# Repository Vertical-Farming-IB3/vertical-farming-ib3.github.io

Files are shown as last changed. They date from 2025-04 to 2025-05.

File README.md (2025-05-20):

# IB3 Plan-T pages site

Deze website is bedoeld voor het bijhouden van de voortgang van het project IB3.
De website is ontworpen en bijgehouden door de studenten BA3ecfs en S2ecfs, en is bedoeld voor alle geïnteresseerden in het vertical farming project. Het is een stappenplan van de huidige realisatie en een presentatie van de behaalde resultaten.

[Project website](https://vertical-farming-ib3.github.io/)

[Link](https://github.com/Vertical-Farming-IB3/Plan-T) naar de hoofdrepository.

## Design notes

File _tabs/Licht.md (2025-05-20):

---
icon: fas fa-lightbulb
order: 3
---

## Inhoud
1. [Introductie](#introductie)
2. [led-selectie](#led-selectie)
3. [Spectrum en kleurverhouding](#spectrum-en-kleurverhouding)
    - [Blauw licht (450-460 nm)](#blauw-licht)
    - [Rood licht (560-670 nm)](#rood-licht)
    - [Far-red licht (720-740 nm)](#far-red-licht)
    - [Photosynthetic Photon Flux Density (PPFD)](#photosynthetic-photon-flux-density-ppfd)
        * [Sla en basilicum](#sla-en-basilicum)
        * [Koriander](#koriander)
        * [PPFD-berekening](#ppfd-berekening)
4. [Elektrisch Dimensioneren](#elektrisch-dimensioneren)
5. [Aangeraden Instelling](#aangeraden-instelling) 
6. [Afstand en uniformiteit](#afstand-en-uniformiteit)
7. [Fotoperiode](#fotoperiode)
8. [Thermische berekeningen led-PCB](#thermische-berekeningen-led-pcb)
9. [Ontwerp](#ontwerp)
10. [Uitvoering](#uitvoering)
11. [Afgewerkt product](#afgewerkt-product)
11. [Bronnen](#bronnen)

## Introductie

Bij Team Licht werken we aan led-verlichtingssystemen die speciaal zijn afgestemd voor de vertical farm. Ons huidige project richt zich op de teelt van snijsla en groene kruiden zoals basilicum, koriander en munt. De nadruk ligt op een efficiënte systeem met voldoende Photosynthetic Photon Flux Density (PPFD), afgestemd op bladgroenten. 

## led-selectie

Om de juiste leds te bepalen hebben we ons gebaseerd op het uitgebreid onderzoek van vorig en de expertise van het team van Labo Licht. We hebben voor leds gekozen met een uniforme lichtverdeling voor optimale groei van de planten in de vertical farm. Zo zijn we uitgekomen bij de volgende Cree leds: 

| Type | Kleur | Golflengte (nm) | PPF (µmol/s⁻¹) | View Angle (°) |
|---|---|---|---|---|
| JE2835ARY  | Royal Blue  | 450–460 | 1.01 | 124 |
| JE2835AHR  | Photo Red | 650–670 | 0.72 | 121 |
| JE2835AFR  | Far-Red | 720–740 | 0.72 | 121 |

## Spectrum en kleurverhouding

De keuze van lichtkleuren is cruciaal voor het sturen van de fotosynthese, bladontwikkeling en
morfologie. Dit project gebruikt drie spectraalkleuren:

### Blauw licht (450–460 nm) {#blauw-licht}

Bevordert bladontwikkeling, fotomorfogenese, pigmentvorming en compactheid van de plant.
Het helpt overmatige strekking voorkomen door de plant laag te houden en de stengels stevig te maken.

### Rood licht (650–670 nm) {#rood-licht}

Stimuleert fotosynthese en draagt sterk bij aan biomassavorming. Rood licht is bijzonder efficiënt in de activering van chlorofyl.

### Far-Red licht (720–740 nm) {#far-red-licht}

Hoewel far-red licht buiten het fotosynthetisch actieve spectrum (PAR) valt, draagt het bij aan
het Emerson-effect, waarbij de combinatie van rood en far-red licht leidt tot een verhoogde
fotosynthetische efficiëntie [1]. In dit ontwerp wordt far-red licht daarom in beperkte mate
toegepast. Aangezien de focus ligt op bladgroei en niet op de reproductieve fase (zoals bloei of
zaadvorming), is het nodig om te veel Far-Red licht te vermijden. Een te hoog percentage van Far-Red 
licht zal het process van voortijdig schieten bevorderen, wat ongewenst is bij de teelt
van bladgewassen. De planten kunnen er ook zwak van worden om ze te snel in de hoogte zullen groeien en de stengels hierdoor te smal worden.

### Photosynthetic Photon Flux Density (PPFD)

PPFD, uitgedrukt in µmol m⁻² s⁻¹, meet het aantal fotosynthetisch actieve lichtfotonen dat een
plantoppervlak bereikt. Dit is essentieel in vertical farming, waar kunstlicht de enige bron van
energie is voor fotosynthese.

#### Sla en basilicum

- PPFD van 250 µmol m⁻² s⁻¹ is optimaal voor biomassa, kwaliteit en energiegebruik.
- 200 µmol m⁻² s⁻¹ volstaat bij hoge plantdichtheid (680 planten/m2).
- PPFD spectra verdeling: R:60% FR:20% BL:20% (Dit zijn **NIET** de waardes om in te stellen via HomeAssistant, zie verder)
  
#### Koriander

- PPFD van 250–300 µmol m⁻² s⁻¹ bevordert biomassatoename en antioxidantproductie.
- Optimale prestaties bij verhoogde worteltemperatuur en CO2.
- PPFD spectra verdeling: R:60% FR:20% BL:20% (Dit zijn **NIET** de waardes om in te stellen via HomeAssistant, zie verder)

Aanbevolen richtlijn: Voor bladgewassen is 200–250 µmol m⁻² s⁻¹ geschikt, afhankelijk vanruimtegebruik en teeltstrategie. Voor de verdeling van deze PPFD raden we volgend startpunt aan R:60% FR:20% BL:20% (dit komt **NIET** overeen met de procentuele waardes van de sliders op het Home Assistant dashboard! Zie "Aangeraden Instelling" voor meer info)

#### PPFD-berekening

Voor een en lade van 0.1 m² met 12 blauwe, 20 rode en 16 far-red leds geldt:

PPFD<sub>totaal</sub> = (12 × 1.01) + (20 × 0.72) + (16 × 0.76)  
= 12.12 + 14.4 + 12.16 = 38.68 µmol/s  

PPFD = 38.68 / 0.1 = 386.8 µmol/m²/s

## Elektrisch Dimensioneren

De volgende tabel toont de elektrische karakteristieken van de individuele leds.

| **led Specifications (CreeLed)** | **Far-Red (FR)** | **Red (R)** | **Blue (B)** |
|---|---|---|---|
| **Wavelength (nm)** | 720–740 | 650–670 | 455 |
| **Current (mA)** | 140 | 140 | 140 |
| **Voltage (V)** | 2.2 | 2.15 | 2.96 |
| **Consumption (W)** | 0.308 | 0.301 | 0.414 |

Omdat de driver tot 24V kan voorzien kunnen we 2 led-PCB's in serie plaatsen. De serie verbinding van FR, R en B leds worden dus doorverbonden en het aantal LEDs en spanning wordt hierdoor verdubbeld. Om aan voldoende PPFD output te voldoen, hebben we gekozen om 2 van deze serie connecties per lade te plaatsen. Hieronder zie je een illustratie van de opstelling.

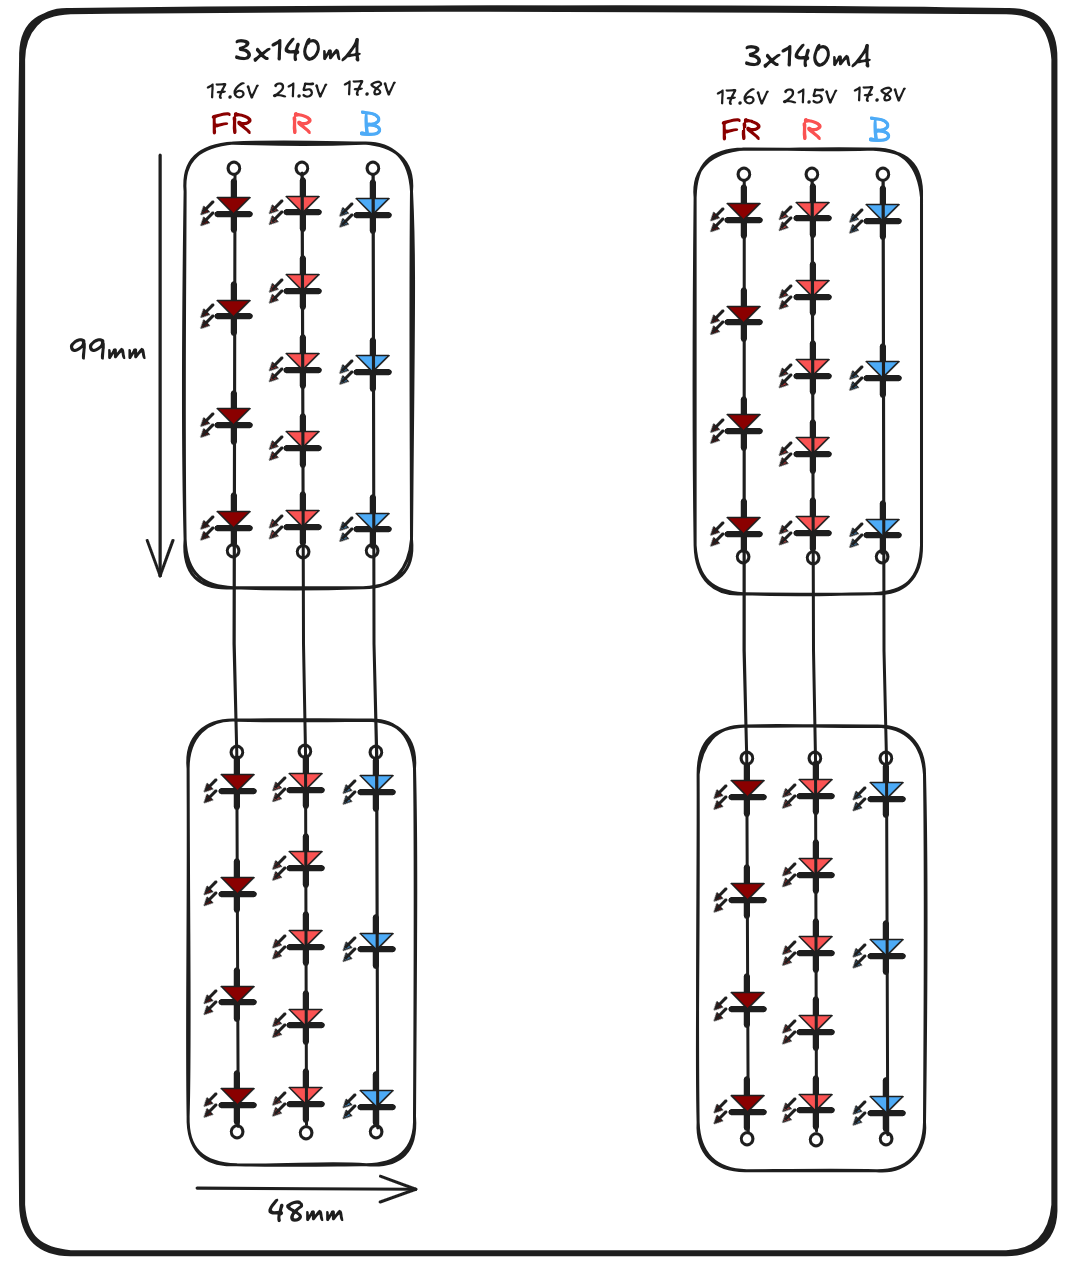
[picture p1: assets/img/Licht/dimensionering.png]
dimensionering led-pcb's


**De specificaties die één led-Driver moet voorzien (dus twee LED-PCB's in serie)** zijn hieronder gegeven, per licht spectra. Alsook de specificatie van één lade (van 2 series van elk 2 PCB's, dus 4 PCB's in totaal)

| | FR | R | B | Per serie| Per Lade|
|---|---|---|---|---|---|
| **Aantal leds** |  8 |  10 | 6 | _ | _ |
| **Voltage (V)**  | 17.6  | 21.5  | 17.76  | — | — |
| **Current (mA)** | 140 | 140 | 140 | 420 | 840 |
| **Consumption (W)** | 2.5 | 3 |  2.5 | 8 | 16 |

- Ratio R:B = 20 divided by 12 ≈ 1.67
- Ratio R:FR = 20 divided by 16 = 1.25

In de volgende tabel staan de PPF/PPFD outputs van elk lichtspectra **voor één lade**.

| | FR | R | B | Totaal|
|---|---|---|---|---|
| **PPF (umol s⁻¹)** | 13.4 | 15.2 | 12.2 | 40.8 |
| **PPFD, 0.1m², 80% (µmol m⁻² s⁻¹)** | 120 | 136 |  110  |  366 |

De waarde in bovenstaande tabel zijn berekend uitgaande van bepaalde voorwaarden die moeilijk vast te stellen zijn, de resultaten zullen dus niet helemaal de werkelijkheid zijn, ze dienen om een idee te geven over de output.

## Aangeraden Instelling
Via de Home Assistant Dashboard kan je per lade het lichtspectra instellen aan de hand van sliders.

Voor goede plantgroei raden we volgende waardes aan om in te stellen:
- Rood: 100%
- Diep Rood: 40%
- Blauw: 40%

Dit zorgt voor (ongeveer) volgende PPF outputs per spectra:
- Rood: 136 µmol m⁻² s⁻¹
- Diep Rood: 47 µmol m⁻² s⁻¹
- Blauw: 44 µmol m⁻² s⁻¹

Dit is een goed startpunt, hieruit kan dan beslist worden om meer of minder diep-rood of blauw toe te voegen afhankelijk van hoe de plantegroei vordert. Als de planten te veel in de hoogte toenemen en slappe stengels hebben, verhoog dan het blauwe licht en/of verlaag het diep-rode licht. Het rode licht kan best altijd op 100% staan voor maximale fotosynthese.

## Afstand en uniformiteit

De leds worden op 25–30 cm boven het gewas geplaatst. Dankzij de brede uitstralingshoek
(121–124°) ontstaat een egale belichting. De kast is voorzien van een witte coating die fungeert
als reflectieve achtergrond en zo schaduwvorming vermindert.

## Fotoperiode

Een cyclus van 16 uur licht en 8 uur donker (16L/8D) is toegepast, wat bewezen effectief is voor
bladgroenten.

## Thermische berekeningen led-PCB

Uit de berekeningen blijkt dat de totale thermische weerstand zonder koeling vrij hoog is, wat resulteert in
 een junctietemperatuur van net boven de 70°C. Dit is wel onder de maximaal toegelaten waarde van 125°C
 die weergegeven wordt in de datasheet, maar om de betrouwbaarheid en levensduur van de led te verbeteren
 is extra koeling aangewezen. Door toevoeging van een koelplaat wordt de junctietemperatuur verlaagd tot
 ongeveer 46°C, wat zorgt voor een veilige marge. Zo zal de led aanzienlijk langer kunnen functioneren zonder
 door te branden.

📄 [Thermische berekeningen (PDF)](https://vertical-farming-ib3.github.io/assets/files/Licht/thermische_berekeningen-1.pdf)

## Ontwerp

Voor het ontwerp van de led-PCB is bewust gekozen voor een compact formaat. Door kleinere printplaten te gebruiken, kan de lichtspreiding beter worden beheerst en afgestemd op de omstandigheden. Elke led-PCB bevat:
- 3 blauwe leds
- 5 rode leds
- 4 far-red leds

De afvoering van de warmte heeft veel aandacht gekregen, vooral omdat dit vorig jaar een groot probleem was. We hebben we de leds in serie met elkaar verbonden aan de hand van brede copper pours aangezien een groot deel van de warmte door de anode en cathode gedissipeerd wordt. Deze copper pours zijn identiek aan de bottom layer van de PCB geplaatst zonder silk screen, deze zijn dan met Via's verbonden met de top layer. De bottom layer en zijn copper pours wordt zo ontworpen dat er één heatsink over geplaatst zal worden. Bij het testen zien we dat de leds heel goed gekoeld worden, wat een grote verbetering is met de led-PCB's van vorig jaar.

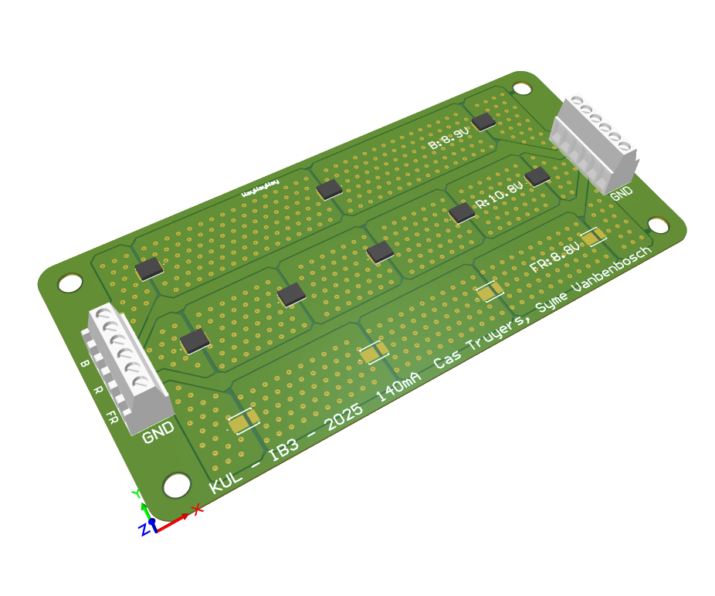
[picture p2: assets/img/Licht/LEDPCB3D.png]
PCB-ontwerp van de led-PCB


Voor het aansturen van de leds is een aparte driver-PCB ontworpen. Per lade is één driver-PCB nodig, waarop maximaal zes led-PCB’s kunnen worden aangesloten. Dit biedt flexibiliteit: er kan eenvoudig wit licht worden toegevoegd of het lichtniveau verhoogd worden door extra led-PCB’s te installeren.

De driver-PCB bevat drie drivers en een ESP32-microcontroller voor de aansturing. De voedingsspanning bedraagt 24V, waarbij een LDO-regelaar wordt gebruikt om de ESP32 van 3,3V te voorzien.

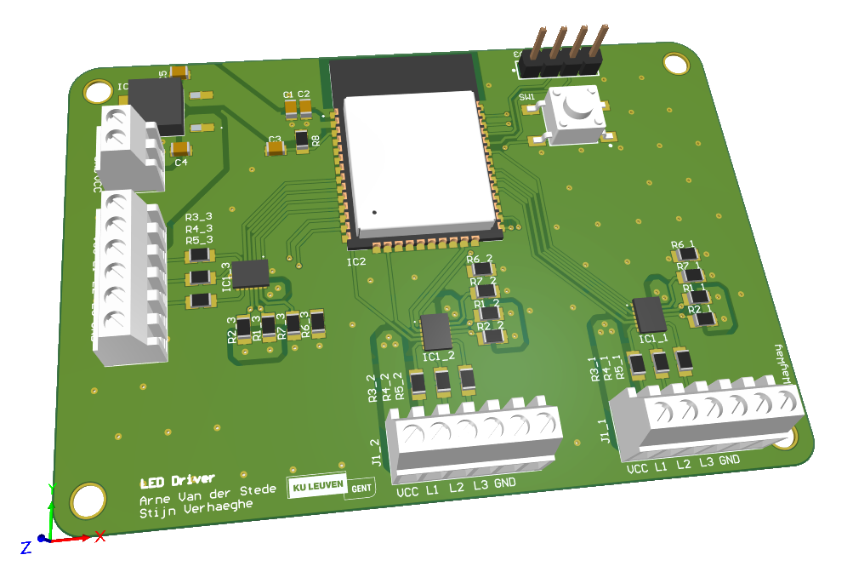
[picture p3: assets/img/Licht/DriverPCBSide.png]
PCB-ontwerp van de Driver-PCB


Voor de verbinding tussen de led-PCB’s en de driver-PCB’s wordt gebruikgemaakt van terminal blocks, wat zorgt voor een eenvoudige en robuuste aansluiting.

## Uitvoering

De verlichting wordt toegepast in lades van 45,7 cm x 38 cm (0.174 m²). Elke lade bevat uiteindelijk 4 PCB’s met:
- 3 blauwe leds
- 5 rode leds
- 4 far-red leds
  
Totaal per lade: 12 blauwe, 20 rode, 16 far-reds.

<div style="display: flex; justify-content: center; gap: 1px; align-items: center; text-align: center;">
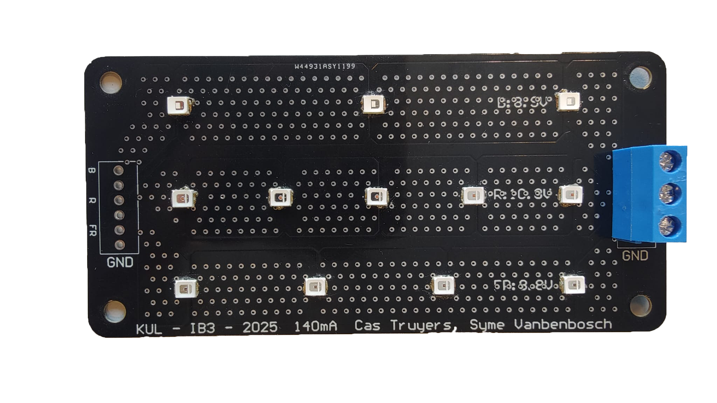
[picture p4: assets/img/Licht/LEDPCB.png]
led-PCB Realisatie
    
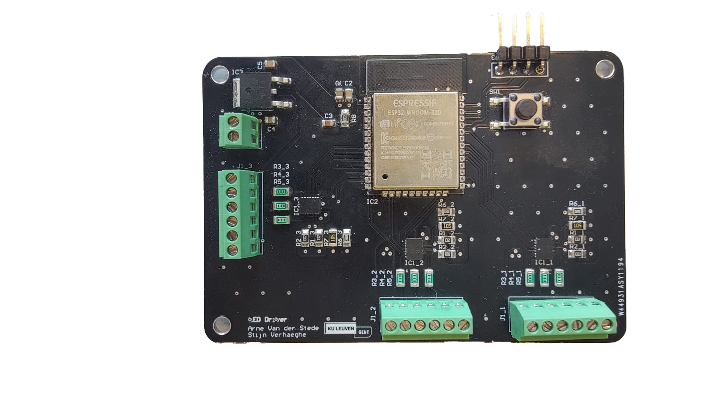
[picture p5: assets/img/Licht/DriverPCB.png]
Driver-PCB Realisatie
    
</div>

## Afgewerkt product

In de kast worden er 2 lades voorzien met verlichting in.

## Bronnen

📄 [Led keuze motivatie (PDF)](https://vertical-farming-ib3.github.io/assets/files/Licht/Leds_keuze_motivatie-2.pdf)
📄 [Documentatie driver (PDF)](https://vertical-farming-ib3.github.io/assets/files/Licht/Documentatie_driver.pdf)

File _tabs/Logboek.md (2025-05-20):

---
icon: fas fa-calendar-check
order: 6
---

# 🌱 Vertical Farm Project "Plan-T" Logboek

---

## Sem 1: Voorbereidende fase

---

### 📸 Concepttekeningen
<div style="display: flex; gap: 10px;">
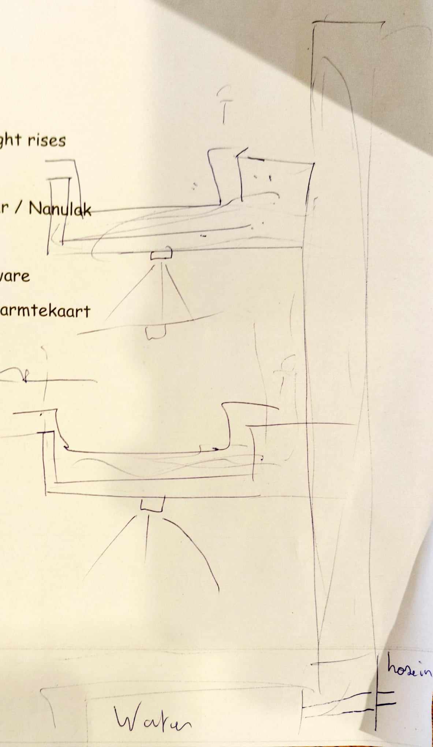
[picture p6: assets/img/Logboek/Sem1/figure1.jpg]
  
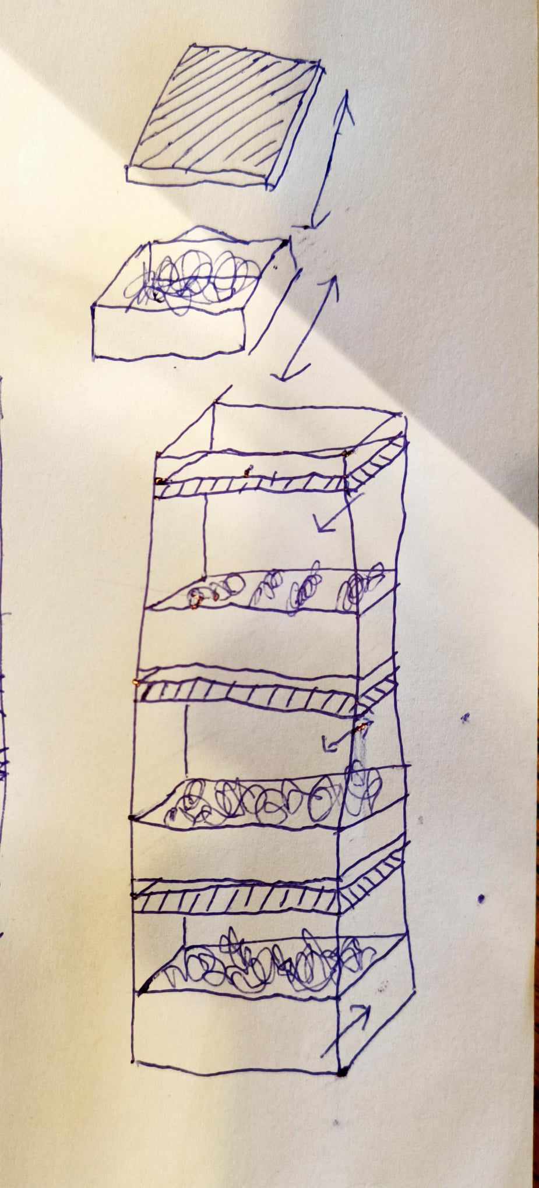
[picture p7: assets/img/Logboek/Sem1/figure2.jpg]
  
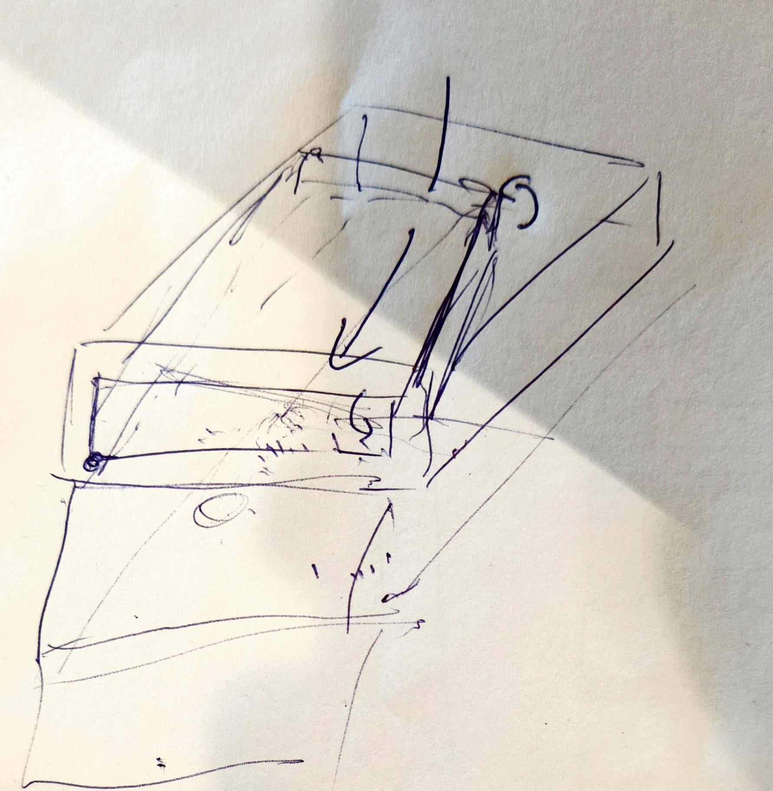
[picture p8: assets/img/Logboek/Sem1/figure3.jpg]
  
</div>

---

### 📅 16-10-2024: Brainstorming 💡
#### 🔄 Herstellen van het oude systeem
- **Vervangen van de drainage**.
- **Upgraden van de relays**.
- **Test van alternatieve substraten**.
- **Verbeteren van waterafvoer**.

#### 🏡 Nieuw systeem: Focus op modulariteit
We mikken op het **ontwerpen van een huisvriendelijke vertical farm**, geen industrieel ontwerp. Ons systeem moet **modulair** zijn.
- **Lade gebaseerd systeem** in een andere lade.
- **Sensoren geconnecteerd via de I2C bus**. <!---->
- **Gemeenschappelijke voedingsmodule** voor alle modules.
- **Plug-and-Play-systeem** voor een makkelijke setup.

#### 📅 Doel van de volgende sessie
- Het opstarten van het oude systeem.

---

### 📅 22-10-2024: Werken aan het oude systeem ⚙️
We verzamelden om het vorige systeem te **analyseren en herstarten**.

#### 🔌 Opstarten van het systeem
Gebruik makende van [deze handleiding](https://verticalfarmib3.github.io/inhoud/operation/), hebben we alles ingeschakeld:
- **ESPHome server** draait op `192.168.0.40:8123` van het CM3-netwerk. <!-- CM3-->
- **Grafana interface** is bereikbaar via poort `3000`.
- **Licht, pompen, ventilatoren en de mixer** zijn succesvol getest.
- **Automatisering** verzekert het in- en uitschakelen van het licht op de juiste ogenblikken.

#### 📦 De constructie herlocaliseren
1. Verwijderen van de **houten constructie**.
2. Het **glazen paneel** uit elkaar gehaald.
3. Het schoonmaken van **de oude planten en het interieur**.
4. Verplaatsen van het **houten frame**.
5. Installeren van het **aluminum frame**.

#### 🌱 Nieuwe zaadjes
We plantten verse zaadjes:
- Basilicum
- Dille
- Bieslook
- Oregano
- Peterselie
- Afrikaanse goudsbloemen

📌 **Geüpdatet lichttiming**: **08:00 - 20:00**
📌 **Geüpdatet ventilatortiming**: **5 minuten elke 30 minuten**

#### ❌ Gevonden problemen
- ⚠️ De mixer werkt slechts **enkele seconden** aan een stuk.
- ⚠️ **De drainage verstopt** door de rotswol.
- ⚠️ **Hete lijm was gebruikt** in de plaats van waterbestendige silicone.
- ⚠️ **Hoge opstartstroom** zorgt voor het aan elkaar lassen van de relaiscontacten.
- ⚠️ **Kapotte vochtsensoren** leiden tot overbewatering en lekken.

---

### 📅 19-11-2024: Planning fase 📝
Wachtende op onze **PCB's** hebben we:
- Een planning gemaakt
- Een taakverdeling gemaakt
Er is beslist om, voor een efficiënte realisatie van het project, een aantal gespecialiseerde teams op te delen.
Nl. een team plantenbak (sensoren bij de planten), water (toe- en afvoer), licht (groeilampen) en power (centrale voeding).
Het integreren zal dan met alle groepen samen gebeuren.

---

### 📅 17-12-2024: Presentatie & feedback
We stelden onze vooruitgang voor en vergaarden feedback in onze **ClickUp notities**.

---

## Sem 2: Praktische fase

---

### 📸 Concepttekeningen
<div style="display: flex; gap: 10px;">
  <!-- Tekeningen en 3D-modellen toevoegen -->
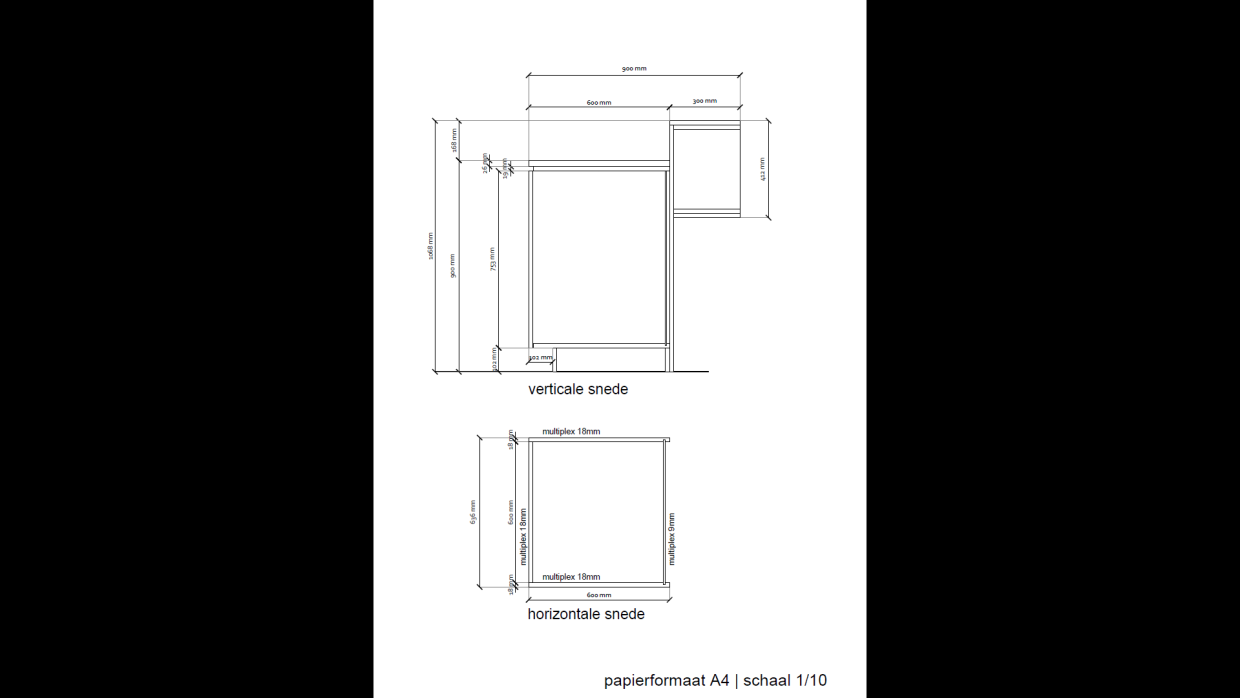
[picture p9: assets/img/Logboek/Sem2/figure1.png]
  
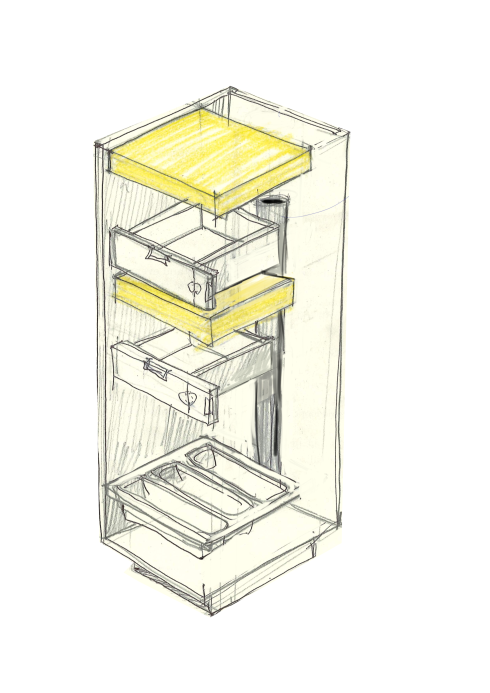
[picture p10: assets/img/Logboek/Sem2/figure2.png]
  
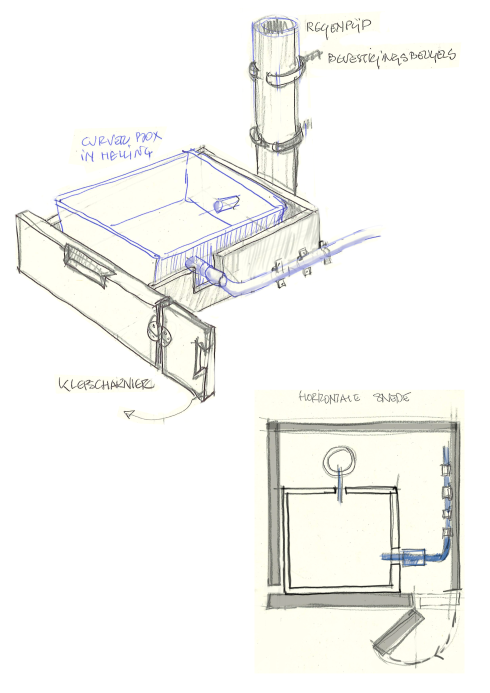
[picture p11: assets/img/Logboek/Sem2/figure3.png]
  
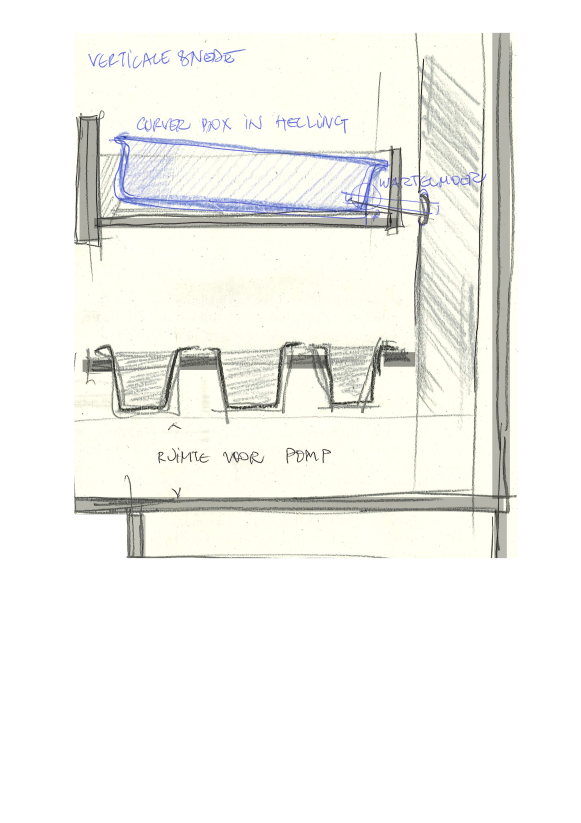
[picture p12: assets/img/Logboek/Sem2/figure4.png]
Concept 4
  
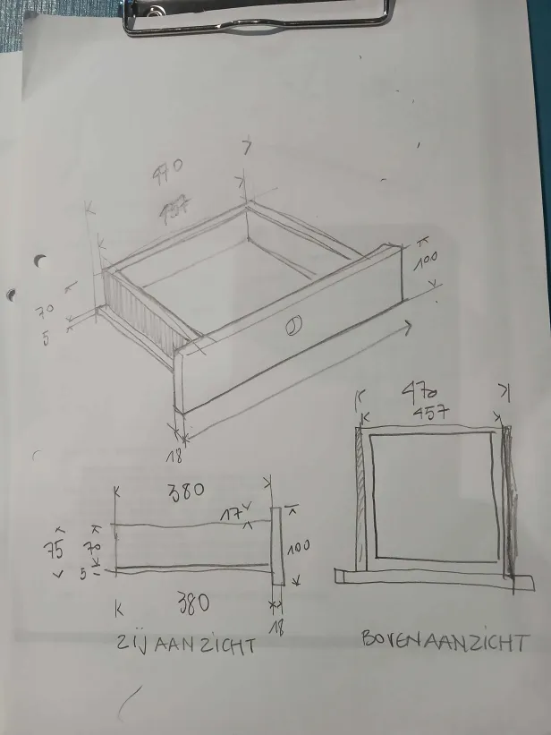
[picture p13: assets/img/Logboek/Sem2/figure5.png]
Concept 5
  
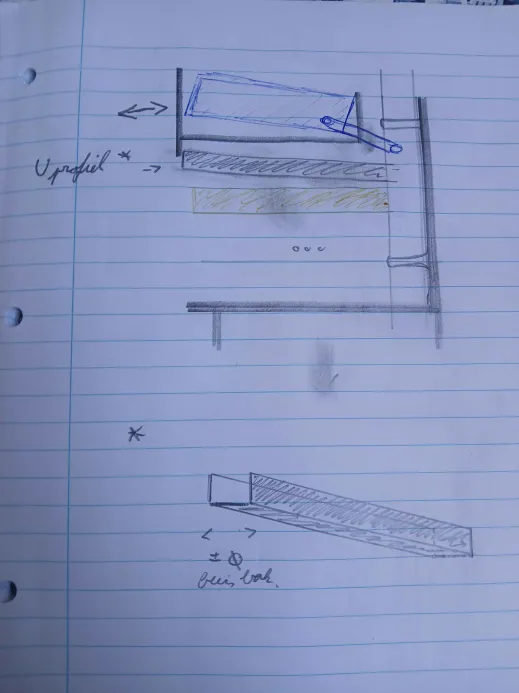
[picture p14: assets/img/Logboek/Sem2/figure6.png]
Concept 6
  
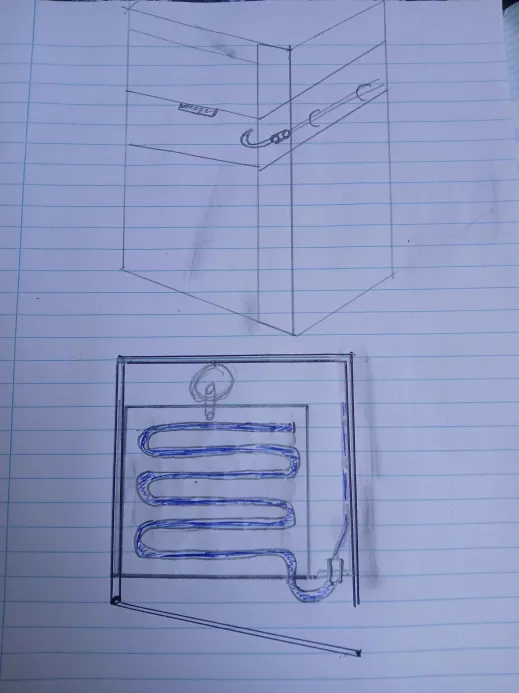
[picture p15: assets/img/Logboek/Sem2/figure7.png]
Concept 7
  
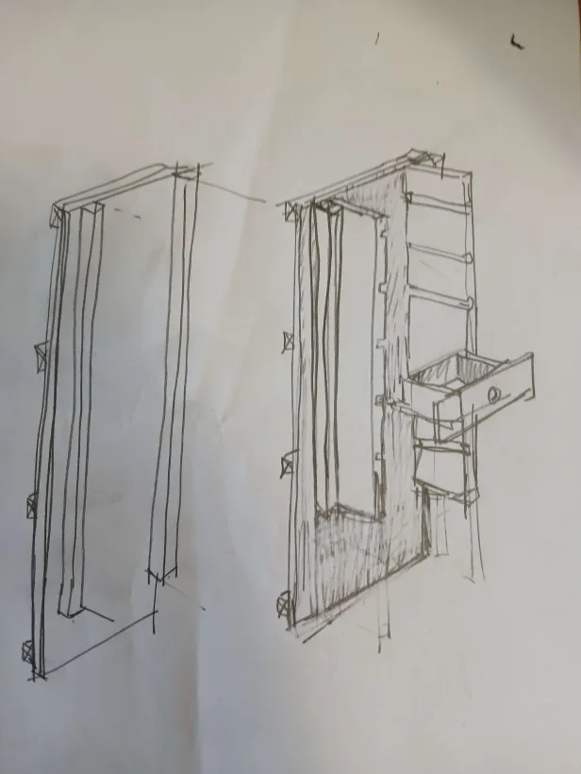
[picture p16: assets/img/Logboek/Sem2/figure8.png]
Concept 8
  
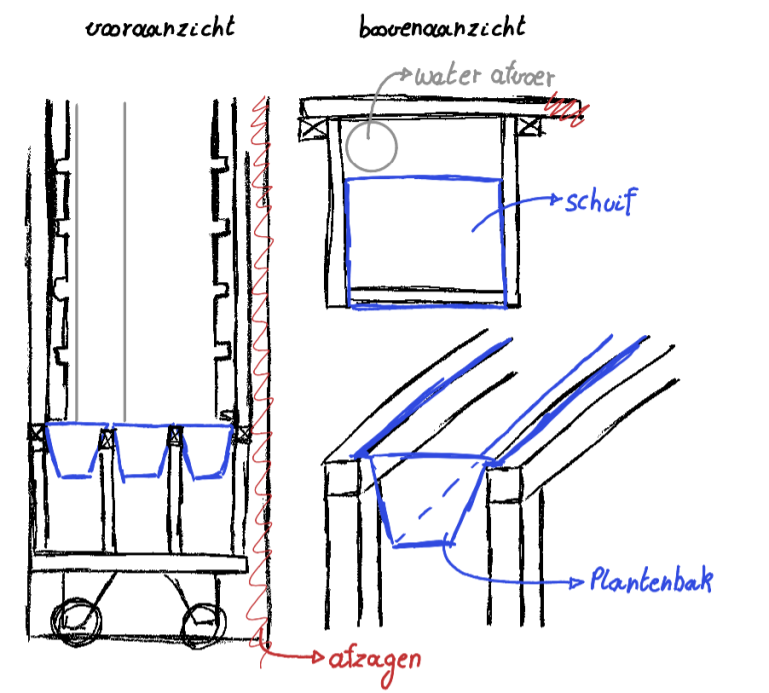
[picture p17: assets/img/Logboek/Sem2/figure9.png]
Concept 9
  
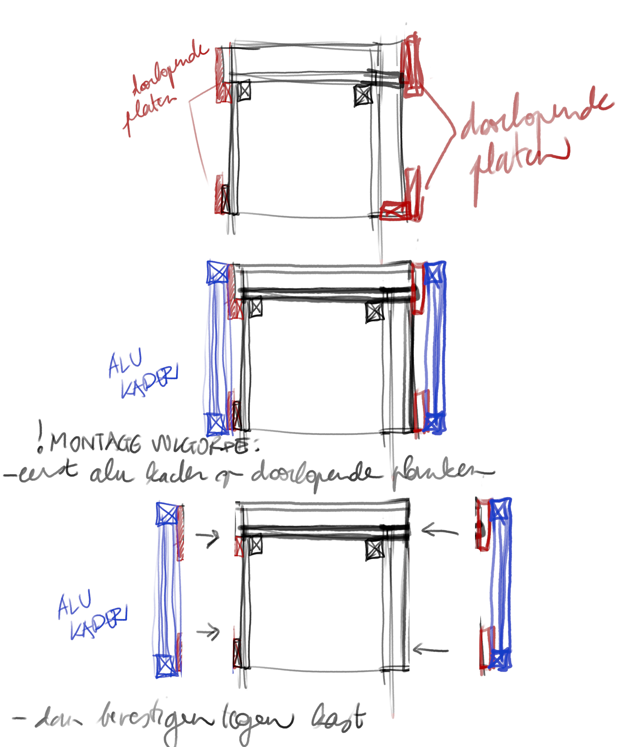
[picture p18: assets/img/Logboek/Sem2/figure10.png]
Concept 10
  
</div>

---

### 📅 Dinsdag 11-02-2025: De voorbereiding begint

Iedere groep (Team Plantenbak, Team Licht, Team Water) zijn begonnen met onderzoek en het ontwerpen van hun systemen. 
- We **hergebruikten zoveel mogelijk componenten** van de oude constructie.

##### Team Water: 
-	Teamverdeling schakels (+ herverdeling) + inlichten
-	Opstellen taakverdeling
-	Afwerken planning 
-	Besluiten welk systeem te gebruiken 
-	Bestellijst aanvullen

##### Team Plantenbak: 
- Teamverdeling (NFC en Plantenbak/Sensoren)
- Planning opstelling voor ons team
- Onderzoek naar sensoren, substraat, verluchting, planten, ...
- Bestelijst aanvullen
- Overleg met team water over watersysteem
  
##### Team Licht: 
- Teamverdeling (code, led PCB en driver PCB)
- onderzoek naar drivers, leds, ...
- Planning opstelling voor ons team

---

### 📅 Dinsdag 18-02-2025:
##### Team Water: 
-	Afronden bestellijst en opsturen 
-	Voeding bepaald
-	Onderzoek naar ADC voor de chemische probes
-	Start elektrisch schema PCB
-	Afwerken planning + indienen
-	Uitwerken toevoer/afvoer

##### Team Plantenbak: 
- Bepalen van sensoren
- Bestelijst afwerken
- Onderzoek naar NFC systeem
- Elektrisch schema voor PCB tekenen
- Uitdenken van vorm en manier om alle sensoren, ventielen, substraat, ...
  te verwerken in de plantenbak
- Vervoldigen planning van team plantenbak

##### Team Licht: 
- bepalen van leds + overleggen met mensen van licht over aantal leds en kleur
- bepalen van driver, datasheets lezen
- onderzoek koeling driver
- Bestelijst afwerken
  
---

### 📅 Dinsdag 25-02-2025: Eerste bestelling geplaatst! 🛒
We bestelden meerdere benodigde componenten voor onze constructie.
#### 📦 Gebruikte websites:
- Mouser
- RS Components
- TinyTronics
- PCBWay
- AliExpress

##### Team Water: 
-	Elektrisch schema verder afwerken
- Water schema afwerken
- Start binnenkast
-	Componenten besteld
-	Bedrijfsbezoek Colruyt

##### Team Plantenbak:
- Elektrisch schema verder afwerken
- Helpen met ontwerpen binnenkast
- Begin ontwikkeling NFC systeem
- Start van testen beschikbare sensoren
- Bestellijst indienen
- Bedrijfsbezoek Colruyt

##### Team Licht:
- Led en driver PCB design
- lezen datascheet driver + start code schrijven
- thermische berekeningen
- Bestellijst indienen
- Bedrijfsbezoek Colruyt

##### Team Power:
- Overleg met alle teams
- conectoren en voedingen kiezen
- bestellijst indienen
  
---

### 📅 Dinsdag 04-03-2025: Eerste zaaisel! 🌱 
##### Team Water: 
-	Elektrisch schema afgemaakt
-	PCB maken gestart
- Binnenkast opouwen  
-	Afbreken en recycleren oud systeem met team plantenbak
-	Bedrijfsbezoek Citymesh

##### Team Plantenbak: 
We zaaiden onze eerste zaadjes als een referentie, of misschien wel om ze binnenkort in onze werkende vertical farm te verpotten! 
### 🌿 Geplant:
- Basilicum
- Koriander
- Munt
- Oregano
- Bladsla

Bijkomend hebben we, 
- De oude constructie afgebroken.
- PCB ontwerpen
- Verder NFC systeem ontwikkelen
- Bedrijfsbezoek Citymesh

##### Team Licht:
- Led en driver PCB design
- code verder schrijven
-	Bedrijfsbezoek Citymesh

---

### 📅 Dinsdag 11-03-2025: PCB's besteld! 🎉
De PCB's zijn besteld bij **PCBWay**.

##### Team Water: 
-	Elektronische componenten testen
-	PCB-componenten gecontroleerd en PCB besteld
-	Pinout voor PCB beschreven
-	YAML voor watersysteem gestart
-	Gewerkt aan opbouw kast met team plantenbak

##### Team Plantenbak:
- Verder ontwikkelen van NFC systeem
- Beschikbare sensoren verder testen
- Algemene YAML code schrijven voor de plantenbak
- Gewerkt aan opbouw kast met team water
- PCB afgewerkt en gecontroleerd
- Opstarten van de github pages (website)

##### Team Licht:
- PCB afgewerkt en gecontroleerd
- Code verder schrijven
- Voorbereiden levering PCB
  
---

### 📅 Donderdag 13-03-2025:
##### Team Water: 
-	Overleg met chemie (meneer De Vreese)

---

### 📅 Zaterdag 15-03-2025: Wachten op bestellingen & voorbereiden opendeurdag 
##### Team Water: 
-	UV-C Lamp testen 
-	Bekijken wat nodig voor chemie
-	Verder werken aan YAML-code

##### Team Plantenbak: 
Met de meeste componenten besteld en Mr. Coppens die aan de kast werkt, werken wij aan:
- Het testen van sensoren, ESP's en YAML-code.
- Verder schrijven aan de algemen YAML-code voor de platnebakken
- Het zoeken naar bijkomende materialen: witte verf, verfborstels, kokosvezels, etc.---
- Volledig in orde brengen van de template voor de github pages (website)
- NFC verder ontwikkelen

##### Team Licht:
- CSBE challenge
- bestellen heatsinks en thermal pads
  
---

### 📅 Dinsdag 18-03-2025: De echte constructie komt dichterbij! :hammer:
##### Team Plantenbak: 
- Naar de Action om verf, borstels en andere benodigdheden.
- Verder werken aan de github pages (website)
- YAML-code verder schrijven
- NFC systeem verder ontwikkelen
- Extra planten gezaaid
- Overleg met team water voor uitwerking watersysteem in plantenbak

##### Team Water: 
- Kalibratie van de ion-sensoren nagekeken.
- YAML-code afgewerkt
-	Afgewerkt kastframe met team plantenbak
- Stroomsensoren
  
##### Team Licht: 
- LDO bestellen
- Voorbereiding componenten PCB
- Code verder schrijven

---

### 📅 Donderdag 20-03-2025:
##### Team Water: 
-	Chemie: kalibratievloeistoffen gemaakt

---

### 📅 Vrijdag 21-03-2025: Een kast om in te werken 🎆
##### Team Water: 
-	Kast afgewerkt met team licht
-	Kast verplaatst naar B225

---

### 📅 Dinsdag 25-03-2025:
##### Team Water: 
-	Verder gewerkt aan kast (indeling uitgewerkt, laden gerepareerd, …)
-	Materiaal gekocht in de Gamma
-	Oude profielen uit elkaar gehaald en nieuwe profielen in elkaar gezet
-	Plantenbakken hellend gemaakt
-	Indeling uitgedacht van de la 
-	PCB's gesoldeerd
-	Probehouder ontworpen en geprint
  
##### Team Plantenbak: 
- PCB's solderen
- Kast wit schilderen
- NFC systeem verder ontwikkelen
- YAML-code verder schrijven
- 3D prints voor in platenbak ontwerpen
- In overleg de indeling van de plantenbak verder uitgedacht
- Extra aanpassingen aan de algemene structuur van de github pages (website)

##### Team Licht: 
- bestukken led PCB's 
- uittesten led PCB's
- Code verder schrijven

---

### 📅 Woensdag 26-03-2025: 
##### Team Water: 
-	Ultrasone sensorhouders ontworpen en geprint
-	PCB programmeren en verbinden met HomeAssistant

---

### 📅 Dinsdag 01-04-2025:
##### Team Water: 
-	Chemische probes gekalibreerd
-	Stroomsensor gekalibreerd
-	Documentatie kalibraties op Github aangevuld
-	Probes, pompjes, tubes gemonteerd en aangesloten
-	Hoogtesensoren gemonteerd
-	Afvoeren in plantenlades bevestigd
-	Pompen aangesloten 
- Buizen leggen voor de toevoer

##### Team Plantenbak: 
-	Elektronica samen beginnen brengen
-	Sensoren afhankelijk testen via yaml
-	3D-print ontwerpen om onze elektronica in te steken en een houder voor NFC-kaarten

##### Team Licht: 
- bestukken driver PCB's 
- uittesten driver PCB's
- Code verder schrijven

---

### 📅 Vrijdag 04-04-2025:
##### Team Water: 
-	Nagekeken realisatie buitenkast

---

### 📅 Paasvakantie: 07-04-2025 tot en met 20-04-2025
##### Team Water: 
- Verder gewerkt aan afvoer: montage + boren regenpijp
- Gekeken naar buitenkast
- Nagemeten kapotte probe
- Test op lekkages + lekken opgelost
- Waterproofen
- Hoogtesensoren aangesloten en gekalibreerd
- Houder voor middelste hoogtesensor ontworpen
- Kabels in kabelhulzen gestoken
- Kraantjeswater en voedingsstoffen uitgemeten
- Reservoirs gevuld, pompjes getest, mixer getest, circulatie getest

##### Team Plantenbak: 
- Houdersysteem voor plantenpotjes gemaakt
- Volledig elektronicasysteem verbonden en getest
- Lang bugfixen op probleem bij relais (Schottky-diode)
- Nieuwe batch plantjes gezaaid

##### Team Licht: 
- Led-PCB's monteren in de lades
- Driver + led-PCB's samen testen
- Code verder schrijven

---

### 📅 Dinsdag 22-04-2025:
##### Team Water: 
- Site verderwerken
- Power aansluiten PCB van water
- Automatisaties schrijven (circulatie, mengreservoir bijvullen, waarschuwingen laag waterniveau, ventilatie, water pompen naar lades)
- Reservoirs uitkuisen
- Hoogtesensoren op nieuwe brackets gemonteerd
-	Verdergewerkt aan frame
-	Bekeken PH-sensor
-	Acryl gesneden (voorkomen stilstaand water).
-	Samengezeten andere groepen
-	Besproken verdere aanpak project

##### Team Plantenbak: 
- Site verder afwerken
- Elektronica in de bakken gefit
- Dubbele bodem in de bakken gekit 
- Automatisatie schrijven

##### Team Licht: 
- Led + driver PCB's monteren in de lades
- Alle PCB's uittesten en debuggen
- Kleine aanpassingen code + uittesten

##### Team Power:
- Voedingen aan binnnenkast bevestigen
- Fuse en schakelaar aansluiten
- Eerste conectoren solderen
  
---

### 📅 Woensdag 23-04-2025:
##### Team Water:
- Dashboards in Home Assistant beginnen maken
- Connectoren powergedeelte verder geplaatst
  
##### Team Plantenbak:  
- Kabels gelabeld
- Bugfixing: waarom werkt onze schakeling niet meer in de kast?
  - ESP1 heeft plots kortsluiting?
  - ESP2 kan geen verbinding meer maken met esphome

---

### 📅 Donderdag 24-04-2025:
##### Team Water:
- Herkalibratie probes

---

### 📅 Vrijdag 25-04-2025:
##### Team Plantenbak:  
- Bugfixing: beide bakken terug werkende gekregen 

---

### 📅 Weekend 26-04-2025 tot en met 27-04-2025:
##### Team Plantenbak:  
- De bakken een dubbele bodem geven, poging twee ( vorige waren niet waterdicht )
- Solenoid valve werd vervangen door een regentonkraantje
  - De druk van het laagje water was niet groot genoeg om de valve te kunnen sturen

---

### 📅 Dinsdag 29-04-2025:
##### Team Water: 
- pH-probe gekalibreerd en geïntegreerd
- Probleem PCB debuggen en oplossen (Buck converter ground)
- Dashboard Home Assistant afgewerkt (water)
- Website verder aanpassen
- Dimitri helpen met onderkant en linkerzijde kast
- Andere groepen helpen met debuggen
- Start eindpresentatie
- Waterafvoer, eb-vloed lade

##### Team Plantenbak: 
- Elektronica nog een laatste keer testen en in de lades bevestigen
- Verder werken aan de site
- Beginnen aan PowerPoint
- Plantjes in de bakken zetten

##### Team Licht: 
- Driver PCB's debuggen
- Laatste aanpassingen aan code
- PCB etsen van power meting
- Laatste PCB's monteren in lade
- Presentatie verdediging

---

### 📅 Woensdag 30-04-2025: 
##### Team Water: 
- Verder aan waterafvoer plantenlades gewerkt
- Ontbrekende slangklemmen aan pompen bevestigd
- Afwerkingen Home Assistant (verfijning automatisaties/dashboard/...)
- Probleem geïdentificeerd met de aquariumpomp (mixer)

---

### 📅 Dinsdag 06-05-2025: 

- Geïntegreerde test
- Voorbereiding eindpresentatie

##### Team Water: 
- Afwerken Frame buitenkast + start afwerking buitenkast
- Afwerkingen binnenkast
- Site + git
- Testen + verbeteringen
- Werken aan presentatie
- Afwerken power aansluiting
- Afwerken Home Assistant dashboard
- Verderzoeken naar probleem pH en mixer

##### Team Plantenbak: 
- Laatste plantjes in de bakken zetten
- Verder werken aan PowerPoint
- Verder werken aan site
- Sensoren kalibreren

##### Team Licht:
- Lade afwerken en uittesten
- Laatste aanpassingen aan code
- PCB etsen van power meting
- presentatie afwerken

##### Team Power:
- Laatste conectoren solderen
- Krimpkousen over alle connecties plaatsen
  
---

### 📅 Woensdag 07-05-2025: 
##### Team Water en Plantenbak: 
- Ophalen en bevestigen afwerking buitenkast 

##### Team Licht:
- Fixen lade 2

---

### 📅 Donderdag 08-05-2025: 
##### Team Water en Plantenbak: 
- Kast proper maken en volledig installeren voor opendeurdag op zaterdag 

---

### 📅 Vrijdag 09-05-2025: 
##### Team Water, Plantenbak en Licht: 
- De kast getest
- De finale plantjes geplant in de bak
- De rockwolbak werd volledig vervangen door kokosvezel
- De setup klaargezet voor op de opendeurdag (tv etc.)
- Last-minute probleempjes opgelost

---

### 📅 Zaterdag 10-05-2025: 
##### Team Water, Plantenbak en Licht: 
- De kast ligt nu officieel aan. 

---

### 📅 Dinsdag 13-05-2025:
- Update home assistant
- Laatste hand aan de kast
- Eindpresentatie

---

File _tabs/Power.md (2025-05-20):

---
icon: fas fa-plug
order: 4
---

## Inhoud 
1. [Simple and safe](#simple-and-safe)
  - [Fuse](#fuse)
  - [Ingang en hoofdschakelaar](#ingang-en-hoofdschakelaar)
  - [Spanningen](#spanningen)
  - [Connectoren](#connectoren)
  - [Kabels](#kabels)
2. [Energieverbruik en vermogen](#energieverbruik-en-vermogen)
  - [ACS712 Hall-effect stroomsensor (team water)](#acs712-hall-effect-stroomsensor-team-water)
  - [ACS712 module (team plantenbak)](#acs712-module-team-plantenbak)
  - [ZXCT1107 Stroommonitor (team licht)](#zxct1107-stroommonitor-team-licht)
   
## Simple and safe
Als team Power willen we alle groepen op een zo veilig en eenvoudig mogelijke manier van stroom voorzien. Daarnaast moet het voor team Licht en team Plantenbak mogelijk zijn om op verschillende niveaus in de kast stroom af te halen.

### Fuse
Om de kast, de gebruikers en de plaatselijke infrastructuur te beschermen: voorzien we een fuse van 1 ampère aan de ingang. Deze beperkt het maximaal verbruik tot 230 watt [W] en biedt bescherming bij technische defecten.

Afbeelding van een fuse

### Ingang en hoofdschakelaar
De fuse is verwerkt in een connector met ingebouwde schakelaar en een C14-ingang. Dit zorgt ervoor dat het aan en uit schakelen van de kast eenvoudig blijft.

Afbeelding van de ingang

### Spanningen
Om de juiste spanningen te voorzien hebben we eerst samen gezeten met alle teams. Daar ondervonden we dat team licht minstens 24V nodig zal hebben voor de leds, water minstens 12V voor de pompen en team plantenbak minstens 12V voor de ventilatoren. Om het zo eenvoudig mogelijk te houden kozen we om te werken met twee voedingen, de omzettingen naar 3,3V voor de ESP wordt op de PCB zelf gedaan.

Afbeelding van de voeding op de binnenkast

### Connectoren
We gebruiken GX12-4 connectoren, die bevatten 4 pinnen. Hierop worden zowel de 24V als de 12V aangesloten. De connectoren kunnen slechts op één manier worden aangesloten, wat garandeert dat team Plantenbak altijd 12V ontvangt en team Licht 24V. Doordat beide spanningen op dezelfde connector beschikbaar zijn, is het systeem eenvoudig te gebruiken. In totaal zijn er vijf connectoren geplaatst op verschillende hoogtes in de kast.

Afbeelding van de connector

### Kabels
Voor de verbinding tussen de connector en de voedingen gebruiken we een kabel van 0,75mm². Deze kunnen tot 1300W aan, dat is ruim voldoende aangezien de fuse het vermogen begrenst tot 230W.
Tussen de connectoren en de voedingen worden diverse kabeltypes gebruikt, maar met een minimale diameter van 1mm². Aangezien de voedingen maximaal 100,8W leveren, zijn alle gebruikte kabels ruim voldoende gedimensioneerd.

## Energieverbruik en vermogen
Het systeem verbruikt natuurlijk wel wat elektriciteit. Om ons verbruik goed in de gaten te houden, wordt dit per onderdeel apart gemeten en weergegeven via Home Assitant. Zo kan je makkelijk zien waar veel of weinig vermogen wordt gebruikt. Het doel is om zo weinig mogelijk energie te verbruiken, bij het behouden van een optimale werking.

### ACS712 Hall-effect stroomsensor (team water)
<figure>
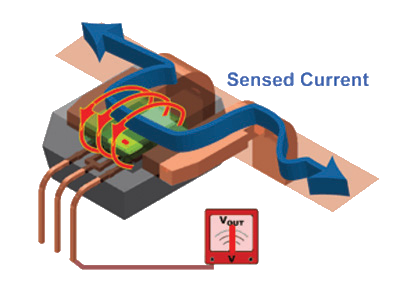
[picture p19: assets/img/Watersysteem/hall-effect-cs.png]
Hall effect
  
  <figcaption>Bron: Hall-effect current sensor, SparkFun, www.sparkfun.com, 29/04/25</figcaption>
</figure>

Voor Team Water gebeurt de vermogensmeting met een hergebruikte sensor van vorig jaar: de ACS712 Hall-effect stroomsensor. Daarbij meten we de stroom die door de voedingskabel van de PCB loopt.

Deze sensor werkt op een galvanisch gescheiden manier, wat de veiligheid bevordert. Wanneer er stroom door de draad vloeit, ontstaat er een klein magnetisch veld rondom die draad. De sensor meet dat veld en zet het om in een analoog signaal dat we uitlezen op [onze PCB](https://vertical-farming-ib3.github.io/Water/#stuurlogica).
De spanning is gekend (een constante 12V) waardoor we door een simpele formule het verbruikt vermogen kunnen berekenen: vermogen = spanning x stroom. 

We voerden een kalibratie uit met deze sensor die [hier](https://github.com/Vertical-Farming-IB3/Plan-T/blob/main/Water/Vermogensmeting.md) terug te vinden is. Bij deze kalibratie merken we op dat er een hogere accuratie behaald wordt bij grote vermogens. Over het gehele meetbereik behalen we een gemiddelde meetfout van 6%.

De UV-C-lamp zit op een afzonderlijke vermogenskring, deze wordt niet rechtstreeks gemeten (hoge spanning!). Er wordt hiervoor een theoretisch verbruik bij de meting opgeteld.

- **Voordelen:**
    - Output eenvoudig in te lezen op een microcontroller
- **Nadelen:**
    - Kan beïnvloed worden door temperatuur en andere EM-uitstraling
    - Meet de bronspanning niet op

### ACS712 module (team plantenbak)
Voor de plantenbakken werd een al gemaakte module gebruikt. Een teamlid had deze thuis nog op overschot en dit bespaarde ons  tijd omdat we zelf geen module moesten maken. Het werkingsprincipe is idem als bij team water: het is een hall-effect stroomsensor.

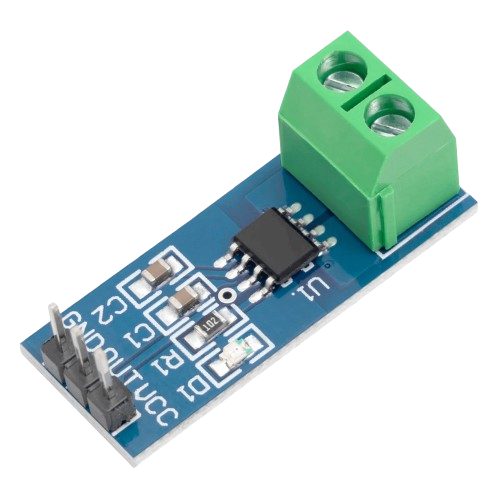
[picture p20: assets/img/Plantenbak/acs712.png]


### ZXCT1107 Stroommonitor (team licht)
Voor team Licht gebeurt de powermeting via een stroommonitor: de ZXCT1107, een high-side stroommonitor van Diodes Incorporated. Alles wordt duidelijk uitgelegd in de bijgevoegde pdf.

 [Powermeting (PDF)](https://vertical-farming-ib3.github.io/assets/files/Licht/powermeting.pdf)

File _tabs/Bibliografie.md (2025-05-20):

---
icon: fas fa-info-circle
order: 8       
---

Onze gebruikte bronnen:

- “Vertical farm - IB3”, Vertical Farm - IB3. https://verticalfarmib3.github.io/
- K. Al-Kodmany en Department of Urban Planning and Policy, College of Urban Planning and Public Affairs, University of Illinois at Chicago, “The Vertical Farm: A Review of Developments and Implications for the Vertical City”, feb. 2018. doi: 10.3390/buildings8020024.
- K.-H. Yeo, G.-L. Choi, J.-H. Lee, K.-S. Park, en K.-Y. Choi, “Development of Nutrient Solution Compositions for Paprika Cultivation in a Closed Coir Substrate Hydroponic System in Republic of Korea’s Winter Cropping Season”, Horticulturae, vol. 9, nr. 4, p. 412, mrt. 2023, doi: 10.3390/horticulturae9040412.
- M. Butturini, L. F. M. Marcelis, en Wageningen University, Horticulture and Product Physiology Group, Wageningen, The Netherlands, “Vertical farming in Europe: Present status and outlook”, in Plant Factory (Second Edition), 2020, pp. 77–78. [Online]. Beschikbaar op: https://doi.org/10.1016/B978-0-12-816691-8.00004-2
- T. Van Gerrewey 1, N. Boon 2, en D. Geelen 1, “Vertical farming: the only way is up?”, Agronomy, vol. 12, p. 2, dec. 2021, [Online]. Beschikbaar op: https://doi.org/10.3390/agronomy12010002
- A. M. Beacham, L. H. Vickers, en J. M. Monaghan, “Vertical farming: a summary of approaches to growing skywards”, The Journal Of Horticultural Science And Biotechnology, vol. 94, nr. 3, pp. 277–283, feb. 2019, doi: 10.1080/14620316.2019.1574214.
- W.-J. Cho, H.-J. Kim, D.-H. Jung, D.-W. Kim, T. I. Ahn, en J.-E. Son, “On-site ion monitoring system for precision hydroponic nutrient management”, Computers And Electronics in Agriculture, vol. 146, pp. 51–58, feb. 2018, doi: 10.1016/j.compag.2018.01.019.
- F. Kalantari, O. Mohd Tahir, R. Akbari Joni, E. Fatemi, en Faculty of Design and Architecture, University Putra Malaysia, Kuala Lumpur, Malaysia, “Opportunities and Challenges in Sustainability of Vertical Farming: A Review”, Journal Of Landscape Ecology, jun. 2017, [Online]. Beschikbaar op: https://10.1515/jlecol-2017-0016
- N. Slingerland, “Wat is het nut van toevoeging van zuurstof in water?”, Horticoop Technical Services, 3 mei 2023. [Online]. Beschikbaar op: https://www.hcts.tech/nieuws/wat-is-het-nut-van-toevoeging-van-zuurstof-in-water/#:~:text=Voordelen,Verlaagt%20stress%20in%20de%20plant 
- “Welke voedingstoffen heeft een plant nodig?”, Pokon, 6 augustus 2024. https://www.pokon.nl/tips/welke-voedingstoffen-heeft-een-plant-nodig-/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,de%20tuin%20als%20in%20huis.
- Wikipedia-bijdragers, “Waterschimmels”, Wikipedia, 2 oktober 2023. https://nl.wikipedia.org/wiki/Waterschimmels
- “Blauwalgen? Melden en maatregelen nemen”. https://vmm.vlaanderen.be/beleid/waterbeleid/kwaliteit-waterlopen/blauwalgen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,lange%20tijd%20ter%20plaatse%20blijven
- I. De Jong, “Hoe bestrijd je groene algen in je aquarium? Tips en oplossingen”, Aquania, 13 maart 2025. https://aquania.nl/blogs/algen/hoe-bestrijd-je-groene-algen-in-je-aquarium-tips-en-oplossingen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,het%20water%20een%20grote%20rol.
- Wikipedia-bijdragers, “Ultrasoonsensor”, Wikipedia, 13 januari 2022. https://nl.wikipedia.org/wiki/Ultrasoonsensor
- Wikipedia-bijdragers, “Ultraviolet”, Wikipedia, 16 april 2025. https://nl.wikipedia.org/wiki/Ultraviolet
- Cleantotaal.nl, “Alles wat u moet weten over UVC licht & desinfectie | Clean Totaal”, Cleantotaal.nl, 19 januari 2021. https://www.cleantotaal.nl/uvc/#:~:text=Wat%20is%20UVC%3F,het%20menselijk%20oog%20waarneembaar%20is.
- Wikipedia contributors, “Hall effect sensor”, Wikipedia, 11 april 2025. https://en.wikipedia.org/wiki/Hall_effect_sensor#:~:text=Hall%20effect%20sensors%20are%20used,them%20to%20measure%20filament%20thickness.
- A. Mazouzi e.a., “Repair of UV-Induced DNA Damage Independent of Nucleotide Excision Repair Is Masked by MUTYH”, Molecular Cell, vol. 68, nr. 4, pp. 797-807.e7, nov. 2017, doi: 10.1016/j.molcel.2017.10.021.
- “Thephoto-protectiveroleofvitaminDinthe microalgaEmilianiaHuxleyi”, jun. 2024. Geraadpleegd: 25 februari 2025. [Online]. Beschikbaar op: https://www.cell.com/action/showPdf?pii=S2589-0042%2824%2901106-4
- “UV-C Sani”. https://www.ozoneuv.co.za/uv-c-sani.html
- Nikki, “Optimale bodem PH-waarde”, Organifer | Organische Meststoffen & Plantversterkers, 6 september 2023. https://organifer.com/nl/optimale-bodem-ph-waarde/
- “Waterkwaliteit in jouw gemeente | Farys”. https://www.farys.be/nl/watersamenstelling-en-hardheid-in-jouw-gemeente
- “Green Boots biologische plantenvoeding voor groenten | Action BE”, Action.com. https://www.action.com/nl-be/p/3004917/green-boots-biologische-plantenvoeding-voor-groenten/
- T. Deseyn, “pH zuurtegraad in de moestuin”, Plukkers.com, 25 augustus 2017. https://plukkers.com/blogs/news/ph-zuurtegraad-moestuin#:~:text=Een%20foute%20zuurtegraad%20voor%20een,je%20planten%20te%20weinig%20opnemen.
- “Waterniveau sensor”, TinyTronics. https://www.tinytronics.nl/nl/sensoren/vloeistof/waterniveau-sensor
- “DFRobot Gravity Contactloze vloeistofniveau schakelaar Sensor”, TinyTronics. https://www.tinytronics.nl/nl/sensoren/vloeistof/dfrobot-gravity-contactloze-vloeistofniveau-schakelaar-sensor
- “Ultrasonic Sensor - HC-SR04”, TinyTronics. https://www.tinytronics.nl/en/sensors/distance/ultrasonic-sensor-hc-sr04
- Waterpompshop, “Wat is een dompelpomp en waar wordt deze pomp voor gebruikt?”, Waterpompshop. https://www.waterpompshop.nl/blog/wat-is-een-dompelpomp-en-waar-wordt-deze-pomp-voor-gebruikt
- Koifarm, Luchtsteen voor luchtpomp zuurstof in de vijver. [Online]. Beschikbaar op: https://koifarm.shop/categorie/luchtpompen-voor-vijver/luchtstenen/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,watervolume%20in%20beweging%20wordt%20gebracht.
- “Ademruimte voor je vijver: Alles over luchtpompen”, Tips & Adviezen - Toppy, 7 november 2024. https://www.toppy.nl/advies/189/zo-installeer-je-een-luchtpomp-bij-jouw-vijver.html
- “Pomp & beluchting”. https://www.petsplace.be/nl/vis/pomp-beluchting
- “GY-SCD40 Module - CO2, luchtvochtigheid en temperatuursensor (I2C)”, TinyTronics. https://www.tinytronics.nl/nl/sensoren/lucht/vochtigheid/gy-scd40-module-co2-luchtvochtigheid-en-temperatuursensor-i2c
- “Winsen MH-Z19B CO2 Sensor met kabel”, TinyTronics. https://www.tinytronics.nl/nl/winsen-mh-z19b-co2-sensor-met-kabel
- “Adafruit CCS811 Air Quality Sensor Breakout - VOC and eCO2”, Adafruit. https://www.adafruit.com/product/3566
- “RFID / NFC kit PN532 with S50 card and S50 key tag”, TinyTronics. https://www.tinytronics.nl/en/communication-and-signals/wireless/rfid/rfid-nfc-kit-pn532-with-s50-card-and-s50-key-tag
- “RFID kit MFRC522 + S50 Mifare met kaart en key tag”, TinyTronics. https://www.tinytronics.nl/nl/communicatie-en-signalen/draadloos/rfid/rfid-kit-mfrc522-s50-mifare-met-kaart-en-key-tag
- “NXP MFRC630 Series NFC/RFID Tags & Transponders”, Mouser Electronics. https://gr.mouser.com/c/semiconductors/wireless-rf-integrated-circuits/nfc-rfid-tags-transponders/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
- “ACS712 Stroomsensor Module - 20A”, TinyTronics. https://www.tinytronics.nl/nl/sensoren/stroom-spanning/acs712-stroomsensor-module-20a
- “INA219 I2C DC Current and Voltage meter 3.2A module”, TinyTronics. https://www.tinytronics.nl/en/sensors/current-voltage/ina219-i2c-dc-current-and-voltage-meter-3.2a-module
- “AC Stroom Sensor - SCT013-030 (30A)”, TinyTronics. https://www.tinytronics.nl/nl/sensoren/stroom-spanning/ac-stroom-sensor-sct013-030-30a
- “Capacitive Soil Moisture Sensor module (with cable)”, TinyTronics. https://www.tinytronics.nl/en/sensors/liquid/capacitive-soil-moisture-sensor-module-with-cable
- “YL-69 Nieuwe Smart Elektronische Bodem Probe Vocht Hygrometer Detectie Vochtigheid Sensor Module Voor Arduino Board Diy Robot Slimme1 Auto”, AliExpress. https://nl.aliexpress.com/item/1005004305871722.html   
- “Soil Temperature-Moisture Sensor SHT10”, Gotron. https://www.gotron.be/soil-temperature-moisture-sensor.html

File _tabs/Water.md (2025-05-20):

---
icon: fas fa-droplet
order: 2
---

## Inhoud
1. [Introductie](#introductie)
2. [Componentenlijst](#componentenlijst)
3. [Stuurlogica](#stuurlogica)
4. [Controle](#controle)
    - [Ultrasoonsensor](#ultrasoonsensor)
    - [UV-C](#uv-c)
    - [Eindloopschakelaar](#eindloopschakelaar)
    - [Probes](#probes)
5. [Toevoer](#toevoer)
    - [Reservoirs](#reservoirs)
    - [Tubes](#tubes)
    - [Quick connectors tubes](#quick-connectors-tubes)
    - [Pompaansturing](#pompaansturing)
        - [Waterpomp](#waterpomp)
        - [Luchtpomp en luchtsteen](#luchtpomp-en-luchtsteen)
        - [Onderwaterpomp](#onderwaterpomp)
6. [Afvoer](#afvoer)

## Introductie
Om plantjes te laten groeien zijn water en voedingsstoffen onmisbaar. Met Team water staan wij in voor het aanvoeren en afvoeren van deze voedingsoplossing met de juiste kwaliteit. Dit gebeurt via een slim watersysteem dat instaat voor het mengen, verdelen en recupereren van het water.

In de volgende secties bespreken we elk onderdeel van dit systeem in meer detail.

## Componentenlijst
Hier vindt u de benodigde componenten voor het Project, voor dit onderdeel kan u kijken bij sectie Team Water binnen de bestellijst.

📄 [Bestellijst (Excel)](https://vertical-farming-ib3.github.io/assets/files/BOM.xlsx)

## Stuurlogica
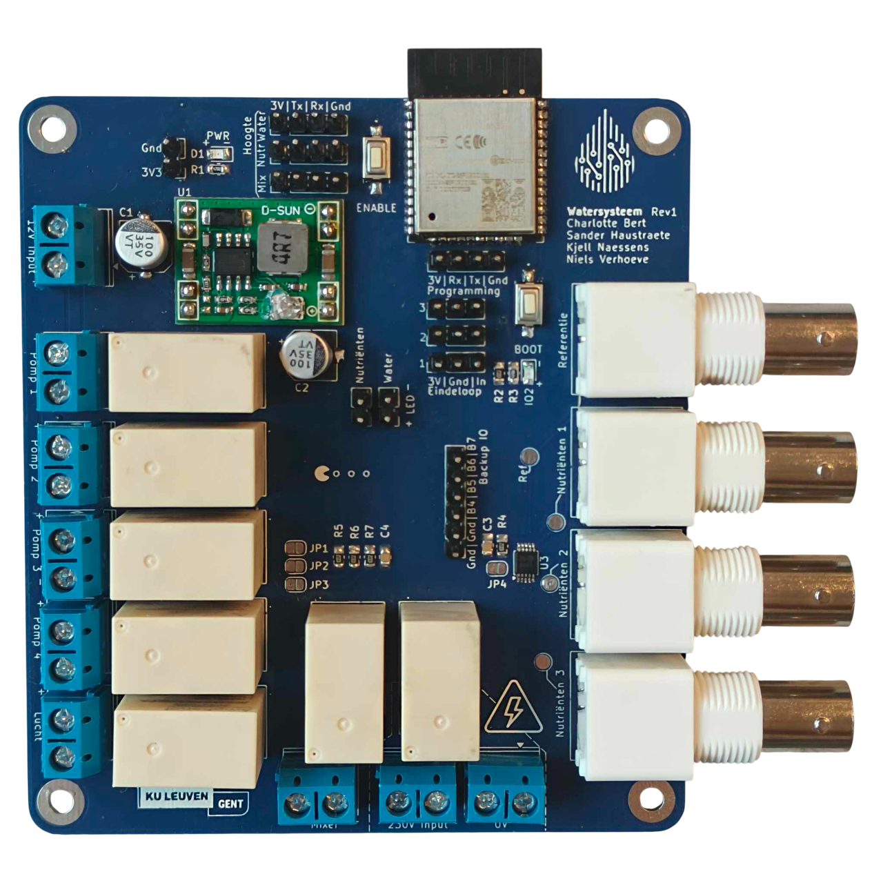
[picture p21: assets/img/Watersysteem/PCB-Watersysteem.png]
Afbeelding van de PCB


Afbeelding van de PCB met connecties

Het Printed Circuit Board (PCB) van het watersysteem moet een hele reeks inputs en digitale outputs verzorgen:
- Inputs
    - (Analoog)  Chemische probes: 3 probes + 1 referentieprobe d.m.v. externe 16 bit ADC (I<sup>2</sup>C)
    - (Analoog) PH-probe (met BNC-Controller)
    - (Digitaal) Ultrasone hoogtesensoren: 3 sensoren
    - (Digitaal) Eindeloopschakelaars: 1 sensor (we voorzagen 3 aansluitingen)
    - (Analoog)  Stroommeting: 1 onboard ADC-input
- Outputs
    - Status leds: 2 leds (1 package)
    - Onboard led voor debuggen: 1 led
    - UV-C lamp: 230V relais
    - Mixer: 5V relais
    - Luchtpomp: 12V relais
    - Waterpompen: 4 x 12V relais

We maakten gebruik van een IO-expander (MCP23017) die aan te sturen is via I<sup>2</sup>C. Het uitlezen van de analoge probes vereist een ADC met hoge resolutie. Hiervoor maken we gebruik van een 16-bit ADC (ADS1115), ook uitgelezen via I<sup>2</sup>C. Het bijhouden van het energieverbruik gebeurt met een Hall-effect stroomsensor, verder besproken in Power.

<iframe src="{{ '/assets/html/ibom_watersysteem.html' | relative_url }}" width="100%" height="600px" sytle="border:none;"></iframe>

Meer informatie over de PCB, zoals het schema en de pin-out vindt u [hier](https://github.com/Vertical-Farming-IB3/Plan-T/blob/main/Water/PCB/){:target="_blank"}.

**Software** 

We maken gebruik van Home Assistant in combinatie met ESPHome. Op onze microcontroller staat code die gegenereerd wordt via ESPHome. We beschrijven deze code in een [YAML-bestand](https://github.com/Vertical-Farming-IB3/Plan-T/blob/main/Water/PCB/watersysteem.yaml). Dankzij de koppeling met Home Assistant kunnen we zeer makkelijk iedere component uitlezen en aansturen. Het aansturen van de componenten gebeurt aan de hand van 'automatisaties'. De automatisaties en het uitlezen van de data gebeurt via een lokale server die alle systemen samenbrengt. Deze data wordt dan samengebracht op een dashboard die de gebruiker kan raadplegen.

## Controle
### Ultrasoonsensor
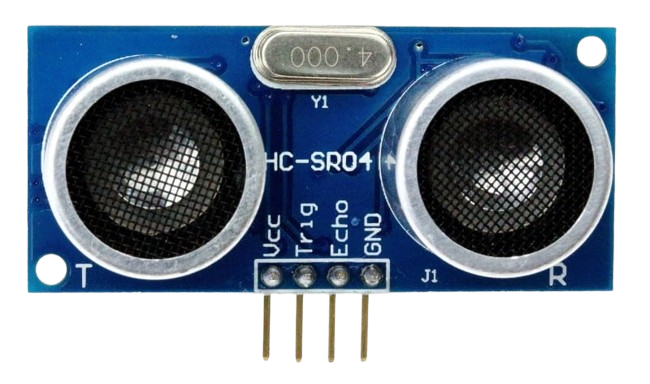
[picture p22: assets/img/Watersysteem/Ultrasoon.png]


De [ultrasoonsensor](https://www.tinytronics.nl/nl/sensoren/afstand/ultrasonische-afstandssensor-rcwl-1604){:target="_blank"} wordt gebruikt om de hoogte van het waterniveau in een reservoir te meten. Dit doet hij met behulp van geluidsgolven: de sensor zendt een ultrasone geluidspuls uit en meet de tijdsduur tot het signaal, na weerkaatsing door het wateroppervlak, terug wordt opgevangen. Op deze manier wordt de afstand tot het water berekend — zonder dat er fysiek contact nodig is.

We hebben voor deze sensor gekozen na verschillende overwegingen:
- Contactloos meten: dit voorkomt slijtage en problemen met het vuil worden van de sensor in het water.
- Analoge meting: dit maakt het mogelijk om de hoogte van het waterniveau te meten en niet alleen 'vol' of 'leeg'.
- Geschikt voor water en voedingsstoffen: hij werkt ook betrouwbaar als er voedingsstoffen in het water zijn opgelost.
- Voedingsspanning van 3.3V<sub>DC</sub> tot 5V<sub>DC</sub>: dit past binnen het bereik van ons systeem.
- Meetbereik van 2 tot 400 cm met een nauwkeurigheid van ongeveer 3 mm.
- Goede prijs-kwaliteitverhouding: de sensor is nauwkeurig en betaalbaar.

📄 [Research waterniveau](https://github.com/Vertical-Farming-IB3/Plan-T/blob/main/Water/Research.md#waterniveau-sensor){:target="_blank"}

Dankzij deze eigenschappen bleek de ultrasone sensor een geschikte keuze voor onze toepassing.

In het kort lijsten we nog even de voor- en nadelen op:
- **Voordelen:** 
    - Nauwkeurige meting van vloeistofniveaus
    - Geen direct contact met het water (minder slijtage en onderhoud) 
    - Eenvoudig te integreren in het systeem
    - Geschikt voor gebruik in diverse omgevingen (kan in verschillende vloeistoffen worden gebruikt)
    - Weinig onderhoud nodig

- **Nadelen:** 
    - Kan interfereren met oneven wateroppervlak
    - Kan gevoelig zijn voor interferentie van obstakels in de omgeving
    - Vereist een geschikte verwerking van het signaal voor juiste interpretatie
    - Beperkte nauwkeurigheid bij hoge luchttemperaturen of luchtstromingen

### UV-C
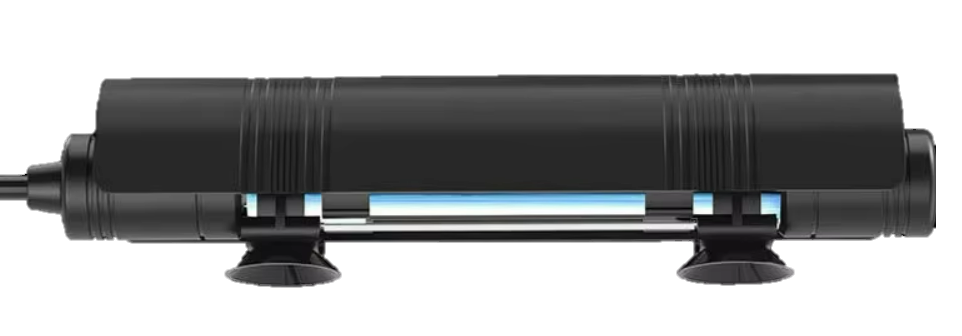
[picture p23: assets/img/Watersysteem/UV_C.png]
Afbeelding van de UV_C


De [UV-C sterilisator](https://nl.aliexpress.com/item/1005006110975582.html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){:target="_blank"} bevindt zich in het mengreservoir. In dit reservoir wordt het terugstromende water uit het systeem ontsmet, voordat het opnieuw naar de planten wordt gepompt. Op die manier blijft het water schoon en vrij van schadelijke micro-organismen.

De UV-C sterilisator werkt met ultraviolet licht van het type C (UV-C). Dit licht heeft een zeer korte golflengte en is krachtig genoeg om het DNA van micro-organismen zoals bacteriën, schimmels en algen te beschadigen. Door deze schade kunnen ze zich niet meer vermenigvuldigen, waardoor ze onschadelijk worden. In een gesloten systeem zoals bij een vertical farm is dit erg belangrijk. Zonder UV-C zouden bacteriën of algen zich via het gerecupereerde water makkelijk kunnen verspreiden, wat schadelijk kan zijn voor de planten.

Let wel op: UV-C verwijdert geen vuildeeltjes of zichtbare vervuiling uit het water. Het maakt het water wel microbiologisch schoon.

- **Voordelen:**
    - Effectieve en chemievrije watersterilisatie
    - Verlaagt de kans op algen- en biofilmvorming
    - Compact ontwerp, makkelijk te integreren
    - Continu gebruik mogelijk zonder extra onderhoudsproducten
- **Nadelen:**
    - Werkt enkel in helder water (verminderd effect bij troebelheid)
    - Beperkte levensduur van de UV-lamp (~8000 uur)
    - Kan gevaarlijk zijn bij directe blootstelling aan mens of dier (goede afscherming vereist)

Ook voor dit systeem zijn meerdere opties bekeken, 1 daarvan is een systeem waarbij het water pas werd ontsmet vlak voordat het naar de plantjes stroomde. Dit zou echter de groei van algen in het reservoir zelf niet voorkomen, omdat het water daar dan nog niet behandeld was. 

De huidige UV-C lamp is gekozen om zijn voldoende vermogen om het nutrientrijke water te ontsmetten, en omdat ze compact genoeg is om in het waterreservoir te plaatsen. Op deze manier kan het water in de mengbak zonder veel extra componenten blootgesteld worden aan het UV-C licht.

📄 [Research ontsmetting](https://github.com/Vertical-Farming-IB3/Plan-T/blob/main/Water/Research.md#ontsmetten-van-mixreservoir){:target="_blank"}

### Eindloopschakelaar
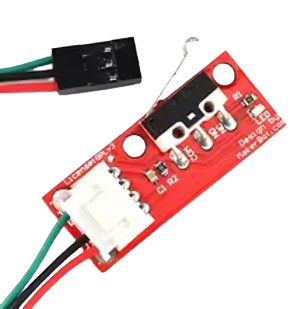
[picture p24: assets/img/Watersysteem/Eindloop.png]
Eindloop


Er is een [eindloopschakelaar](https://www.hobbyelectronica.nl/product/3d-printer-endstop-mechanisch-ramps-1-4/){:target="_blank"} geïmplementeerd om te detecteren of de deur van de Vertical farm open of dicht is. Op deze manier kan de UV-C en sterk licht bijvoorbeeld uitgeschakeld worden bij het openen van de deur, dit voorkomt mogelijk ongemak. Een andere applicatie is het uitschakelen van de pompen, zodat als een la wordt uitgetrokken er geen water in de kast wordt gepompt.

### Probes
Elke plant heeft dezelfde voedingsstoffen nodig (in verschillende hoeveelheden), deze voedingsstoffen zijn opgedeeld in verschillende klassen en zijn gekoppeld aan verschillende concentraties. De primaire voedingsstoffen zijn: Stikstof (N), Fosfor (P) en Kalium (K). Secundaire voedingsstoffen zijn Calcium (Ca), Magnesium (Mg) en Zwavel (S). Hiernaast zijn er ook nog vele micronutriënten. Om de waterkwaliteit in de gaten te houden maken we gebruik van probes (elektroden). We kunnen echter niet voor elk van deze voedingsstoffen een elektrode voorzien, daarom beperken we ons tot een deelset. We kozen voor het gebruik van:

* [Nitraatprobe](https://www.alibaba.com/product-detail/Nitrate-Ion-selective-Electrode-NO3-ISE_60817798149.html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){:target="_blank"}
* [Kaliumprobe](https://www.alibaba.com/product-detail/ISE-K-Potassium-Ion-Selective-Electrode_1600225607843.html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){:target="_blank"}
* [Calciumprobe](https://www.alibaba.com/product-detail/PCa-1-01-Calcium-Ion-Selective_60659669573.html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){:target="_blank"}

Nutrientenprobe

De reden waarom we het calciumgehalte opmeten en niet het fosfaatgehalte is omdat een probe voor het meten van fosfaten veel duurder is in vergelijking met de andere probes. De calciumprobe is geïntegreerd omdat we stevige planten willen kweken in onze vertical farm. Daarnaast verwerkten we nog twee andere probes:

* [PH-probe](https://nl.aliexpress.com/item/1005006063176996.html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){:target="_blank"}
* [Referentieprobe](https://www.alibaba.com/product-detail/232-01-Reference-Electrode-Glass-Shell_60668853882.html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){:target="_blank"}

<p>PH-probe</p>
<p>Referentieprobe</p>

📄 [Belangrijkste karakteristieken Probes](https://github.com/Vertical-Farming-IB3/Plan-T/blob/main/Water/Chemische_probes.md){:target="_blank"}

Dit maakt dat in totaal 5 probes zijn geïntegreerd. De PH-sensor is geïntegreerd omdat verschillende planten houden van een verschillende zuurtegraad van de 'bodem'. De referentieprobe is essentieel voor het uitlezen van de overige probes, belangrijk hierbij is dat ze gevuld is met de juiste referentievloeistof. De overige probes worden gekalibreerd voor ze gebruikt kunnen worden, daarvoor zijn nog enkele componenten nodig, deze zullen we hieronder bespreken. De probes worden uitgelezen aan de hand van ADC-convertoren. De probes zijn temperatuurgevoelig, dit wil zeggen dat bij een verschillende watertemperatuur de probes verschillende meetwaarden kunnen teruggeven bij eenzelfde concentratie. Onze Vertical Farm bevindt zich echter in een omgeving binnenshuis, we gaan er hierbij vanuit dat de temperatuurschommeling in de kast minimaal is. Hiernaast wordt de temperatuur bijgehouden in de plantenbak, deze meetwaarde is voldoende referentie om de probes af te stellen op temperatuurswijzigingen. 

- **Voordelen:**
    - Digitale uitlezing van de aanwezige voedingsstoffen
    - Vereist minder input van de user
    - Uitwisselbaar, indien in de toekomst bijvoorbeeld een fosfaatprobe geïntegreerd wordt
- **Nadelen:**
    - Vereist regelmatige kalibratie
    - Duurder (in vergelijking met manuele testen)
    - Temperatuursafhankelijk

📄 [Kalibratie Probes](https://github.com/Vertical-Farming-IB3/Plan-T/blob/main/Water/Kalibratie_probes.md){:target="_blank"}

## Toevoer
Schematische tekening van het watersysteem

De watertoevoer is zo opgebouwd dat we twee voorraadtanks hebben: één met zuiver water en één met water vermengd met voedingsstoffen. We hebben bewust gekozen om de voedingsstoffen vooraf te mengen met water in het voorraadreservoir, omdat ze in geconcentreerde vorm zeer gevoelig zijn voor bacterie- en algenvorming. De fabrikant raadt aan om slechts één dopje per 8 liter te gebruiken, wat aantoont hoe krachtig het concentraat is.

Beide voorraadtanks zijn uitgerust met een luchtpomp, om de waterkwaliteit stabiel te houden en ongewenste biologische groei, zoals Salmonella en algen, te voorkomen. Elk reservoir heeft ook zijn eigen pomp om het water of de voedingsoplossing naar het mengreservoir te transporteren. In dit mengreservoir worden de vloeistoffen samengebracht en gemixt. Hier zal ook de waterkwaliteit worden opgevolgd.

Vanuit dit centrale punt wordt het water via twee pompen verdeeld naar de plantlades. Aangezien er twee pompen aanwezig zijn, kunnen op dit moment twee lades tegelijk van water worden voorzien

### Reservoirs 
Afbeelding van reservoir

Het watersysteem maakt gebruik van drie reservoirs van 8l. Elk reservoir heeft zijn eigen functie en zorgt ervoor dat de planten altijd de juiste voeding krijgen:

- Waterreservoir: Dit is het reservoir dat zuiver water bevat zonder voedingsstoffen.
- Voedingsstofreservoir: Hierin zitten de voedingsstoffen verdund in water. De voedingsstoffen worden al op voorhand verdund omdat deze anders een te hoge concentratie bevatten.
- Mengreservoir: Dit is het centrale reservoir waar het water en de voedingsstoffen samenkomen. Hier wordt alles gemengd en gecontroleerd op de juiste samenstelling, zodat de planten precies krijgen wat ze nodig hebben.

Elk voorraadreservoir is uitgerust met een luchtpomp die zorgt voor een goede circulatie van het water. Het mengreservoir heeft een aquarium pomp als mixer omdat deze krachtiger is. Daarnaast heeft elk reservoir een ultrasone sensor die het waterniveau meet, zodat je altijd weet hoeveel water er nog beschikbaar is. Elk reservoir heeft ook zijn eigen pomp om het water of de voedingsoplossing naar het mengreservoir te transporteren. Hier zal ook de waterkwaliteit worden opgevolgd. Vanuit dit centrale punt wordt het water via twee pompen verdeeld naar de plantlades. 

De verwerking van de reservoirs binnen ons project is zo ontworpen dat de ze vlot uitneembaar zijn. Dit om reiniging en bijvullen zo eenvoudig mogelijk te houden.

Hier bespreken we nog even kort de voor- en nadelen: 

- **Voordelen:**   
    - Budgetvriendelijk
    - Eenvoudige integratie
    - Makkelijk uitneembaar
    - Goed te reinigen materiaal
    - Voldoende groot volume
- **Nadeel:**
    - Niet afsluitbaar, wat kan zorgen voor vuil en andere verontreinigingen in de reservoires

### Tubes
De [tubes](https://www.tinytronics.nl/nl/mechanica-en-actuatoren/onderdelen/slangen/waterslang-voor-onderwaterpomp-verticaal-horizontaal-3-6v-transparant-1-meter){:target="_blank"} hebben een buitendiameter van 8 mm en een binnendiameter van 6mm. Ze worden gebruikt voor het transport van vloeistoffen tussen de reservoirs en van het mengreservoir naar de plantenbakken. Dankzij hun flexibiliteit zijn ze eenvoudig te installeren, zelfs op moeilijk bereikbare plaatsen. Elke tube is gekoppeld met klemringen en/of quick connectors, zodat ze snel kunnen worden aangesloten en losgemaakt voor onderhoud of aanpassingen. De verwerking van de tubes binnen ons project is ontworpen met oog op modulariteit. Ze kunnen eenvoudig vervangen of aangepast worden zonder dat het hele systeem moet worden herzien.

Hier nog even kort de voor- en nadelen:
- **Voordelen:**     
    - Flexibel
    - Transparant, wat controle van waterflow mogelijk maakt  
    - Compatibel met onze pompen
    - Eenvoudig op maat te knippen
    - Lichtgewicht 
    - Budgetvriendelijk
- **Nadelen:**     
    - Niet geschikt voor hoge druk, geen probleem in ons geval
    - Kan knikken bij scherpe bochten
    - Niet UV-bestendig

### Quick connectors tubes
Afbeelding van de connectors

De [Push-to-Connect koppelingen](https://nl.aliexpress.com/item/1005005808872752.html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){:target="_blank"} worden gebruikt om verschillende buizen of componenten snel en stevig met elkaar te verbinden zonder gebruik van klemmen of lijm.

- **Voordelen:** 
    - Snelle installatie
    - Hergebruikbaar
    - Sterke afdichting 
    - Compact
    - Makkelijke modulariteit
- **Nadelen:** 
    - Slijtage van de sluiting kan zorgen voor lekken over tijd
    - Kan loskomen bij slechte connectie 
    - Complexe handeling nodig bij het verplaatsen van lades

Naast de dubbele connectoren zijn er ook [Push-to-Connect koppelingen](https://nl.aliexpress.com/item/1005008183056175.html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){:target="_blank"} om de buizen af te sluiten, deze worden gebruikt om waterdruk op te bouwen bij de drip irregation, en om leidingen af te sluiten wanneer niet in gebruik. Dit voorkomt lekken en het belanden van vuil in open leidingen. Dezelfde voor- en nadelen zijn geldig als bij de dubbele connector.

### Pompaansturing
De watercirculatie wordt op regelmatige tijdsintervallen geactiveerd om algengroei tegen te gaan. Om de pompen te beschermen, wordt het waterpeil van de reservoirs gemonitord en aangevuld wanneer dit te laag komt te staan. Zo zit er ook een veiligheid ingebouwd die voorkomt dat de pompen activeren wanneer het waterniveau te laag is. De lades worden voorzien van water wanneer zij dit nodig hebben, aan de hand van routines in de [Home Assistant](https://vertical-farming-ib3.github.io/Home-Assistant/){:target="_blank"}. 

#### Waterpomp
1. Twee pompen brengen water en voedingsstoffen vanuit hun respectievelijke reservoirs naar het mengreservoir.
2. Vanuit het mengreservoir transporteren aparte pompen de gemengde vloeistof naar de lades. In de kast is er voldoende ruimte voor twee laden met planten (variërend in hoogte). Om deze reden maken we gebruik van twee pompen voor de toevoer. Aan elke pomp kunnen darmpjes op verschillende hoogtes worden aangesloten, waardoor we een modulair systeem hebben gecreëerd dat eenvoudig uitbreidbaar en aanpasbaar is. De watertoevoer kan gemakkelijk met quick-connectors aan de lades van plantenbak verbonden worden.

Afbeelding van aansluiting pomp

Afbeelding van de waterpomp

Er is gekozen voor deze specifieke pompen omdat ze de beste optie leken voor deze toepassing. Ze zijn sterk en snel genoeg voor onze applicatie met 3m opvoerhoogte; 1,5m aanzuighoogte en  een debiet van 1,8l/min. Ook werken ze op 12V en trekken ze een vermogen in overeenstemming met de specs, de keuze van de voedingsspanning wordt verder besproken in Power. De pompjes zijn relatief goedkoop in vergelijking met alternatieven en andere sites. Bijkomend zijn ze compact en compatibel met andere design keuzes.

#### Luchtpomp en luchtsteen
Afbeelding van de luchtpomp en luchtsteen

Voor het water- en voedingsstofreservoir vindt een combinatie van een [luchtpomp](https://www.tinytronics.nl/nl/mechanica-en-actuatoren/motoren/pompen/luchtpomp-pyp370-12z-12v){:target="_blank"} met een [luchtsteen](https://nl.aliexpress.com/item/1005007443597285.html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){:target="_blank"} plaats om lucht in het water te brengen. Toevoegen van zuurstof aan het water verhoogt de opname van nutriënten, verbetert de wortelontwikkeling en vermindert stress in de plant. Meer zuurstof bevordert echter algengroei, de beweging van het water veroorzaakt door de luchtpomp voorkomt ook algengroei. De groei van algen ontstaat namelijk door verschillende factoren zoals: te weinig stroming, hoge hoeveelheid voedingsstoffen in het water, hoge temperatuur en hoge hoeveelheid licht.

- **Voordelen:**
    - Fijne luchtbellen: betere zuurstofverdeling
    - Voorkomt algenvorming in stilstaand water
    - Energiezuinig systeem
    - Geen directe elektrische belasting in het water (veilig)

- **Nadelen:**
    - Luchtsteen kan verstopt raken
    - Luchtpomp is niet waterdicht
    - Luchtsteen is breekbaar
    - Extra zuurstof kan de algengroei bevorderen 

#### Onderwaterpomp
Afbeelding van de onderwaterpomp

Voor het mengreservoir werd een [onderwaterpomp](https://www.tinytronics.nl/nl/mechanica-en-actuatoren/motoren/pompen/onderwaterpomp-horizontaal-3-6v){:target="_blank"} gekozen om een krachtige, turbulente menging van het water en voedingstoffen te verkrijgen. 

- **Voordelen:**
    - Krachtige pomp voor snelle en efficiënte menging
    - Betrouwbaar bij constant gebruik in water
    - Compact en eenvoudig te integreren in een systeem, geschikt voor zowel horizontale als verticale installatie
    - Energiezuinig

- **Nadelen:**
    - Beperkte capaciteit bij grotere watervolumes (schaalbaarheid)
    - Mag geen lucht aanzuigen, er moet dus een minimumniveau ingesteld worden dat hoger is dan normaal
    - Vereist regelmatig onderhoud om verstoppingen te voorkomen

📄 [Research mixen](https://github.com/Vertical-Farming-IB3/Plan-T/blob/main/Water/Research.md#mixer){:target="_blank"}

## Afvoer
Afvoer

De afvoer van water gebeurt op basis van de zwaartekracht. De lade staat licht gekanteld, zodat overtollig water terugstroomt naar het mengreservoir. Hierdoor is er geen extra pomp nodig voor de afvoer. Om de kast te beschermen tegen waterschade wordt gebruikgemaakt van een centrale pvc-buis. De pvc-buis is deels open gesneden en voorzien van afdekkingen om spatten op te vangen. In deze opening kunnen de plantenbakken dan via een buisje gecontroleerd leeglopen. Als de lade uitgetrokken word willen we niet dat dit water door de kast loopt, om dit probleem op te lossen hebben we ook een module ontworpen met een gootje die onder de lade geschoven kan worden. Bij het uitrekken van de lade zal het water dan via dit gootje in de PVC-pijp belanden. Op deze manier behouden we een hoge mate van modulariteit in het systeem.

Afvoer

Het afgevoerde water wordt niet zomaar geloosd. In het mengreservoir wordt dit restwater gefilterd en gesteriliseerd (door een UV-C lamp en een fijnmazig filter). Nadien kan dit water opnieuw gebruikt worden, eventueel met bijmenging van vers water of extra voedingsstoffen. Dit maakt het systeem duurzaam en circulair, met minimale water- en nutriëntenverspilling.

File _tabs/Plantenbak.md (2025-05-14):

---
icon: fas fa-seedling
title: Plantenbak
order: 1
---

## Inhoud 
1. [Introductie](#introductie)
2. [Componentenlijst](#componentenlijst)
3. [Stuurlogica](#stuurlogica)
4. [Lades](#lades)
   - [Bak 1: flood & drain](#bak-1-flood--drain)
   - [Bak 2: drip hydroponics in kokosvezel](#bak-2-drip-hydroponics-in-kokosvezel)
5. [Sensoren en actuatoren](#sensoren-en-actuatoren)
   - [Soil moisture sensor](#capacitive-soil-moisture-sensor)
   - [Lichtsensor](#bh1750-lichtsensor)
   - [Luchtsensor](#gy-scd40-module)
   - [Plantensoort herkenning](#nfc-reader-pn532)
   - [Energieverbruik monitoren](#acs712-current-sensor)
   - [Ventilatie](#ventilatie)
6. [Materialen](#materialen)
   - [Eurobak](#eurobak)
   - [Regentonkraan](#regentonkraan)
   - [Witte verf](#witte-verf)
   - [Kokosvezel](#kokosvezel)
   - [Plantenvoeding](#plantenvoeding)
   - [Potjes met hydrokorrels en sponsjes](#potjes-met-hydrokorrels-en-sponsjes)
   - [Consumables](#consumables)
7. [Planten](#planten)

---

## Introductie {#introductie}
Als deel van de vertical farm is de plantenbak ontworpen om de groeiomstandigheden van planten optimaal te monitoren. Met deze info kunnen de andere regelsystemen, licht en water, zich aanpassen aan de noden van de planten. Om dit te realiseren zijn volgende sensoren en functies aanwezig.

In de volgende secties bespreken we alle onderdelen van dit systeem in meer detail.

---

## Componentenlijst {#componentenlijst}
Hier vindt u de benodigde componenten voor het Project: voor dit onderdeel kan u kijken bij Team Plantenbak.

📄 [Bestellijst (Excel)](https://vertical-farming-ib3.github.io/assets/files/BOM.xlsx){:target="_blank"}

---

## Stuurlogica {#stuurlogica}
Hier volgt een opsomming van alle in- en outputs van de PCB:
- Inputs
    - (Analoog) [Soil moisture sensor](#capacitive-soil-moisture-sensor) 
    - (Digitaal) [Lichtsensor](#bh1750-lichtsensor)
    - (Digitaal) [Luchtsensor](#gy-scd40-module)
    - (Digitaal) [Plantensoort herkenning](#nfc-reader-pn532)
    - (Analoog) [Energieverbruik monitoren](#acs712-current-sensor)
- Outputs
    - Onboard led voor debuggen
    - [Ventilatie](#ventilatie): 5V relais

Per bak zit één PCB die alle componenten aanstuurt, met als 'brein' een ESP32. Op elke PCB zijn alle GPIO-pinnen naar buiten gebracht, zodat uitbreidingen mogelijk zijn. Deze PCB's zijn ontworpen met KiCAD en geprint door PCBWay. Meer hierover bij de sectie PCB's.

<iframe src="{{ '/assets/html/ibom_plantenbak.html' | relative_url }}" width="100%" height="600px" sytle="border:none;"></iframe>

<!-- Bovenste afbeelding over volledige breedte -->
<div style="display: flex; justify-content: center; width: 100%; margin-bottom: 20px;">
  PCB Front
</div>

<!-- Onderste twee afbeeldingen naast elkaar met gelijke hoogte -->
<div style="display: flex; justify-content: center; align-items: flex-start; width: 100%; gap: 10px;">
  <div style="flex: 1; display: flex; justify-content: center;">
    PCB Back
  </div>
  <div style="flex: 1; display: flex; justify-content: center;">
    Relais Pinout
  </div>
</div>

Meer informatie over de PCB, zoals het schema en de pin-out vindt u [hier](https://github.com/Vertical-Farming-IB3/Plan-T/tree/main/Plantenbak/PCB){:target="_blank"}.

**Software** 

We maken gebruik van Home Assistant in combinatie met ESPHome. Op onze microcontroller staat code die gegenereerd wordt via ESPHome. We beschrijven deze code in een [yaml-bestand](https://github.com/Vertical-Farming-IB3/Plan-T/tree/main/Plantenbak/Software/Plantenbak.yaml){:target="_blank"}. Dankzij de koppeling met Home Assistant kunnen we zeer makkelijk iedere component uitlezen en aansturen. Het aansturen van de componenten gebeurt aan de hand van 'automatisaties'. De automatisaties en het uitlezen van de data gebeurt via een lokale server die alle systemen samenbrengt. Deze data wordt dan samengebracht op een dashboard die de gebruiker kan raadplegen.

---

## Lades {#lades}
Een plantenbak bestaat voornamelijk uit twee onderdelen: een houten lade en een plastic eurobak. De houten lade schuift in de kast, om voor modulariteit te zorgen. De eurobak is de bak waar de planten in groeien. Deze is met een helling in de houten lade bevestigd zodat het water afloopt in de regenpijp achteraan de kast. Er werd voor eurobakken gekozen omdat deze goedkoop en makkelijk te bewerken zijn. In elke lade werd ook een 3D-print bevestigd om de PCB en componenten af te sluiten van de eurobakken. Deze kan [hier](https://github.com/Vertical-Farming-IB3/Plan-T/tree/main/Plantenbak/3D-modellen){:target="_blank"} gevonden worden.

Om de planten te kweken werken we met twee technieken:

•	Flood & Drain (ebb & flow): Hierbij wordt de groeibak periodiek tijdelijk overstroomd met de voedingsoplossing, waarna deze weer terugloopt naar het reservoir. Tijdens de “flood”-fase worden de wortels volledig ondergedompeld, en tijdens de “drain”-fase krijgen ze zuurstof. Dit afwisselend patroon stimuleert wortelgezondheid en efficiënte opname van nutriënten.

•	Drip hydroponics (drip-systeem): Hierbij wordt een voedingsoplossing langzaam en gecontroleerd druppelsgewijs over de wortels van de planten gedruppeld. Dit zorgt ervoor dat de planten altijd toegang hebben tot voldoende water en voedingsstoffen zonder dat er verspilling is.

Doordat we meerdere plantenbakken hebben kunnen we beide technieken testen en onderling vergelijken.

---

### Bak 1: flood & drain {#bak-1-flood--drain}
#### De opstelling:
Deze bak wordt volledig met water gevuld, zodat de wortels van de planten continu ondergedompeld blijven. Ter beveiliging is een overloopsysteem geïntegreerd, dit verhindert dat het waterniveau de rand overschrijdt. De waterafvoer wordt geregeld via een kraan, die een gecontroleerde afloop mogelijk maakt. De plantpotjes worden ondersteund door een rooster, gemaakt uit resthout, waardoor ze eenvoudig in één beweging uit de bak kunnen worden verwijderd. Deze bak heeft bovenaan een quick connector voor watertoevoer, die bevestigd werd met een snelbinder. Er moeten in de eurobak twee gaten gemaakt worden: een voor de overloop en een voor de afloop naar het kraantje. Voor de overloop kan een kort stukje pvc-buis of een 3D-print gebruikt worden. De overloop en de regentonkraan werden vastgemaakt en waterdicht gemaakt met lijm-/afdichtingskit. Er werd over beide gaten een netje gelijmd, zodat er enkel water weg kan.

bak eb flow

---

### Bak 2: drip hydroponics in kokosvezel {#bak-2-drip-hydroponics-in-kokosvezel}
#### De opstelling:
Doorheen deze plantenbak is een flexibel buisje aangebracht dat aan het uiteinde is afgesloten en op regelmatige afstand voorzien is van gaatjes. Dit buisje loopt door het substraat en zorgt voor een gelijkmatige bevochtiging wanneer er water doorheen gepompt wordt. Deze bak heeft ook boven een quick connector die bevestigd werd met een snelbinder. Hier moet maar één gat geboord worden voor de afloop. Daarin werd dan een pvc-buisje in bevestigd met een wartelmoer, en ook hier werd het terug verstevigd en waterdicht gemaakt met lijm-/bevestigingskit. Ook werd bij de uitloop een netje en een metalen raster geplaatst, om zo enkel water door te laten naar de afvoergoot.

drip bak

---

## Sensoren en actuatoren {#sensoren-en-actuatoren}
Voor het kiezen van de sensoren onderzochten we enkele alternatieven. Ons opzoekwerk kan u hier terugvinden: 📄 [Research](https://github.com/Vertical-Farming-IB3/Plan-T/blob/main/Plantenbak/research.md){:target="_blank"}

### Soil moisture sensor {#capacitive-soil-moisture-sensor}
Deze sensor meet het vochtgehalte van het substraat via een analoge pin van de ESP. Dit is een capacitieve sensor, wat betekent dat hij werkt op basis van de verandering in capaciteit van de sensor wanneer deze in contact komt met water. Dit is beter dan een resistieve sensor, omdat deze minder gevoelig is voor corrosie en dus langer meegaat. De PCB van sensor heeft een handige, puntige vorm die het mogelijk maakt om de sensor in de kokosvezel te steken. Een bijkomend voordeel is dat deze sensor al beschikbaar was door IB3 van vorig jaar, dus we hebben ze hergebruikt. Dit hergebruik van componenten draagt bij aan de duurzaamheid van ons project ♻️.

CSMS

---

### Lichtsensor {#bh1750-lichtsensor}
Meet de lichtintensiteit in de kast, om te detecteren of er te veel of te weinig licht is voor de plantengroei. We kozen voor deze sensor wegens de hoge nauwkeurigheid en vooral ook het grote meetbereik. Dit is belangrijk omdat de plantenbak in een afgesloten kast staat, waar de lichtintensiteit kan variëren van donker naar héél fel. Deze sensor wordt gebruikt om te controleren of de planten correct en voldoende (of te veel) belicht worden.

BH1750

---

### Luchtsensor {#gy-scd40-module}
Dit component meet de CO₂-concentratie, de luchtvochtigheid en de temperatuur van de omgeving. Het is een digitale sensor die werkt via I²C. Dit betekent dat hij makkelijk kan worden aangesloten op de ESP-WROOM-32. De sensor heeft een hoge nauwkeurigheid en een snelle responstijd dankzij de photoacoustic-sensing technologie, wat belangrijk is voor de plantenbak. De sensor is ook voorzien van een ingebouwde verwarmingselement, wat helpt om condensatie te voorkomen en de nauwkeurigheid van de metingen te verbeteren. Een klein nadeel van de sensor is dat deze een korte stabilisatietijd heeft van enkele seconden. Ook deze sensors waren al beschikbaar door IB3 van vorig jaar, dus we hebben ze hergebruikt ♻️.

GY-SCD40

---

### Plantensoort herkenning {#nfc-reader-pn532}
Dit gebeurt door interactie met NFC-tags, om per bak te weten welke plant er in de kast zit. Dit is om de kast zo automatisch mogelijk te maken. Als een NFC-tag gelezen wordt, weet de kast welke plant er in de bak zit en kan de routine specifiek voor die plant ingesteld worden. Dit is handig omdat verschillende planten verschillende behoeften hebben qua licht, water en voeding. We kozen voor de PN532, omdat deze al beschikbaar was, want ons weer een nieuwe bestelling bespaarde ♻️.

PN532

---

### Energieverbruik monitoren {#acs712-current-sensor}
Deze sensor is nodig om het verbruik te berekenen aan de hand van de gemeten stroom die het bordje binnenkomt. Dit is een hall-effect sensor die werkt op basis van de verandering in magnetisch veld wanneer er stroom door de draad gaat. Dit is een goede keuze omdat deze sensor al beschikbaar was, wat ons weer een nieuwe bestelling bespaarde ♻️. De sensor heeft een hoge nauwkeurigheid en een snelle responstijd, wat belangrijk is voor het meten van het energieverbruik van de plantenbak.

ACS712

---

### Ventilatie {#ventilatie}
Ventilatie is nodig voor luchtcirculatie, maar ook vooral om plantjes met sterkere en dikkere stengels te kweken. Ook deze ventilatoren waren al beschikbaar van vorig jaar ♻️.

Ventilatoren

---

## Materialen {#materialen}
### Eurobak {#eurobak}
Deze bakken zijn goedkoop, waterdicht en makkelijk te bewerken. Het principe van een bak-in-een-bak (een eurobak in een lade) draagt bij tot de modulariteit.

---

### Regentonkraan {#regentonkraan}
Dit kraantje wordt gebruikt om de afloop van de ebb-and-flow bak te regelen. Deze oplossing werd gekozen omdat de solenoid valve van IB3 van vorig jaar niet werkte. Dit kraantje is een goedkope oplossing omdat het makkelijk te installeren is en goed genoeg werkt.

Regentonkraan

---

### Witte verf {#witte-verf}
Een witte binnenkast zorgt voor optimale reflectie en lichtverdeling in de kast. Dit is belangrijk omdat de plantenbak in een afgesloten kast staat, waar de lichtintensiteit kan variëren. De witte verf zorgt ervoor dat het licht beter wordt verdeeld en dat de planten beter belicht worden. Dit is belangrijk voor de groei van de planten.

---

### Kokosvezel {#kokosvezel}
Een goed biologisch groeimedium voor de planten in de drip-bak. Dit is een goed alternatief voor aarde omdat het een goede waterretentie heeft en de wortels van de planten goed kan ondersteunen. Kokosvezel is ook een duurzaam materiaal omdat het gemaakt is van kokosnootschalen, wat een overvloedig natuurlijk materiaal is. Het is ook biologisch afbreekbaar en kan worden gebruikt als meststof voor andere planten. Dit is een goed alternatief voor rockwol, omdat we daar last hadden van irritatie, te veel waterabsorptie en het was te vast voor de wortels om zich te kunnen nestelen. Kokosvezel was daarom een goede middenweg tussen aarde en rockwol.

Kokosvezel

---

### Plantenvoeding {#plantenvoeding}
Essentiële voedingsstoffen voor gezonde plantengroei. Deze kunnen aangekocht worden in zowat elke tuin/huis/doe-het-zelf winkel. We kozen voor een vloeibare voeding omdat deze makkelijker te doseren is. Dit is volgens ons de goedkoopste en makkelijkste manier om de planten op een goede manier te voeden. Een andere optie was om zelf de chemische stoffen te kopen en deze zelf te mengen, maar dit is veel moeilijker, minder gebruiksvriendelijker en uiteindelijk ook duurder.

Plantenvoeding

---

### Potjes met hydrokorrels en sponsjes {#potjes-met-hydrokorrels-en-sponsjes}
De plantjes kunnen hier in gehangen worden om ze te laten groeien. De open potjes zorgen ervoor dat het water langs de wortels kan lopen.

Potjes

Omdat de plantjes niet zomaar los in het water kunnen hangen, werden er hydrokorrels en sponsjes gebruikt. Deze houden de plantjes vast in de potjes.

Hydrokorrels

---

### Consumables {#consumables}
Zoals schroeven, kabels, soldeermateriaal, 3D-prints, silicone, enzovoort. Dit zijn materialen die we nodig hebben om de plantenbak in elkaar te zetten en te monteren.

---

## Planten {#planten}
We kozen deze soorten:

- Koriander 
- Basilicum 
- Oregano 
- Snijsla 
- Munt
- Bieslook
- Peterselie

<table>
  <thead>
    <tr>
      <th>Plant</th>
      <th>Voordelen</th>
      <th>Nadelen</th>
    </tr>
  </thead>
  <tbody>
    <tr>
      <td>Koriander Koriander</td>
      <td>Snelle groei</td>
      <td>Wordt dun en lang: onstabiel<br>Gevoelig aan verplanten</td>
    </tr>
    <tr>
      <td>Basilicum Basilicum</td>
      <td>Groeit makkelijk<br>Stabiele plant</td>
      <td>Kan snel verwelken</td>
    </tr>
    <tr>
      <td>Oregano Oregano</td>
      <td>Stabiele plant<br>Goed verplantbaar</td>
      <td>Langzame groei</td>
    </tr>
    <tr>
      <td>Snijsla Snijsla</td>
      <td>Erg snelle groei<br>Veel oogst per plant</td>
      <td>Gevoelig voor rot<br>Erg gevoelig aan verplanten</td>
    </tr>
    <tr>
      <td>Munt Munt</td>
      <td>Groeit goed eens ontkiemd<br>Sterke plant</td>
      <td>Woekert makkelijk<br>Ontkiemen duurt relatief lang</td>
    </tr>
    <tr>
      <td>Bieslook Bieslook</td>
      <td>Makkelijk te verplanten</td>
      <td>Langzame kieming</td>
    </tr>
    <tr>
      <td>Peterselie Peterselie</td>
      <td>Kan lang blijven groeien</td>
      <td>Traag kiemproces<br>Wordt lang en dun</td>
    </tr>
  </tbody>
</table>

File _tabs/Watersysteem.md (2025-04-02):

---
# the default layout is 'page'
icon: fas fa-droplet
order: 2
---

> Under construction
{: .prompt-warning }

## Plan
Schematische tekening van het watersysteem

Het systeem bestaat uit onderstaande componenten, aan elkaar gekoppeld:

### Reservoirs:  
Het systeem bevat 1 waterreservoir, 1 voedingsstofreservoir en 1 mengreservoir. Het gerecycleerde water (=water dat terug uit de plantenlades komt) wordt teruggebracht in het watersysteem.  
Het water- en voedingsstofreservoir kunnen aangevuld worden door een klep te openen aan de kast. Elk reservoir bevat een ultrasone sensor om de hoogte van de vloeistof op te meten.  
De luchtstenen (aangevoerd door luchtpompen) in het water- en voedingsstofreservoir circuleren de vloeistof om de groei van algen tegen te houden. In het mengreservoir wordt een aquariumpomp gebruikt om de vloeistoffen te mengen en ook de groei van algen tegen te gaan. In het mengreservoir zit ook een UVC-lamp, als extra maatregel tegen contaminanten (micro-organismen en biologische stoffen).

### Pompen en Pompsysteem:  
Er zijn 2 pompen aanwezig om het water en de voedingsstoffen naar het mengreservoir te brengen. Er is per lade een pomp voorzien om de gemengde vloeistof te transporteren naar de bijhorende lade.

# Compontenten/onderdelen

### Reservoirs:  
Reservoir  
De bloembakken van vorig project worden hergebruikt als reservoirs. Deze zijn ruim genoeg en kunnen makkelijk geïntegreerd worden in het ontwerp.

## Sensoren en Actuatoren

### Waterpomp:  
Waterpomp  
De [waterpomp](https://www.tinytronics.nl/nl/mechanica-en-actuatoren/motoren/pompen/waterpomp-12v){:target="_blank"} heeft een maximale spanning van 12VDC en gebruikt ~400mA (=> P=4,8W). De pomp heeft eenmaxiale opvoerhoogte van 3m en aanzuighoogte van 1,5m. Deze is geschikt voor slangen met ongeveer 6mm binnendiameter.

### Mixer:
Luchtpomp  
Voor het water- en voedingsstofreservoir werd een luchtpomp met luchtsteen gekozen voor de circulatie van het water. Dit wordt gedaan om de groei van algen te voorkomen.

Voor het mengreservoir werd een aquariumpomp gekozen. Dit zorgt voor een sterkere en turbulentere stroom van vloeistof die het water mengt. Deze pomp sturen we aan op basis van de hoogte in het reservoir (om te voorkomen dat de pomp lucht pompt, wat slecht is voor vloeistofpompen)

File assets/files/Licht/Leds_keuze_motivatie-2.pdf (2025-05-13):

## LED-Verlichtingsontwerp voor Vertical Farming van Groene Kruiden

Andres Bosman, Cas Truyers, Daan Vercammen, Stijn Verhaeghe, Syme Vandenbosch, Arne Van der Stede

April 17, 2025

## 1 Inleiding

In dit document wordt een voorstel gepresenteerd voor een LED-verlichtingssysteem binnen een vertical farm, specifiek gericht op de teelt van snijsla en diverse groene kruiden (zoals basilicum, koriander en munt). De nadruk ligt op een effici¨ente en uniforme lichtverdeling met een optimale Photosynthetic Photon Flux Density (PPFD), afgestemd op bladgroenten.

## 2 LED-selectie

Voor dit project zijn drie types LED’s geselecteerd uit de Cree J Series JE2835 Color-reeks:

Table 1: Technische specificaties van geselecteerde LED’s

Type | Kleur | Golflengte (nm) | PPF (µmol/s⁻¹) | View Angle (°)
JE2835ARY JE2835AHR JE2835AFR | Royal Blue Photo Red Far-Red | 450–460 650–670 720–740 | 1.01 0.76 0.72 | 124 121 121

## 3 Spectrum en kleurverhouding

De keuze van lichtkleuren is cruciaal voor het sturen van de fotosynthese, bladontwikkeling en morfologie. Dit project gebruikt drie spectraalkleuren:

Blauw licht (450–460 nm)

Bevordert bladontwikkeling, fotomorfogenese, pigmentvorming en compactheid van de plant. Het helpt overmatige strekking voorkomen [1].

Rood licht (650–670 nm)

Stimuleert fotosynthese en draagt sterk bij aan biomassavorming. Rood licht is bijzonder effici¨ent in de activering van chlorofyl [1].

Far-Red licht (720–740 nm)

Hoewel buiten het PAR-bereik, versterkt far-red in combinatie met rood licht de fotosynthese via het Emerson-effect [1]. Het wordt beperkt ingezet om ongewenst schieten en bloei te vermijden.

Verhouding en doel

Per lade wordt gebruikgemaakt van:

- 12 blauwe LED’s
- 20 rode LED’s
- 16 far-red LED’s

Verhoudingen:

- R:B = 20
12 ≈ 1.67
- R:FR = 20
16 = 1.25

Deze zijn gekozen om zowel compacte groei als effici¨ente fotosynthese te bevorderen, zonder te veel far-red dat tot bloei of strekking kan leiden.

## 4 Far-Red overweging

Hoewel far-red licht buiten het fotosynthetisch actieve spectrum (PAR) valt, draagt het bij aan het Emerson-effect, waarbij de combinatie van rood en far-red licht leidt tot een verhoogde fotosynthetische effici¨entie [1]. In dit ontwerp wordt far-red licht daarom in beperkte mate toegepast. Aangezien de focus ligt op bladgroei en niet op de reproductieve fase (zoals bloei of zaadvorming), is het nodig om overmatige stimulatie van fotosynthese te vermijden. Bij te hoge lichtintensiteit kan dit proces van voortijdig schieten bevorderen, wat ongewenst is bij de teelt van bladgewassen.

## 5 Photosynthetic Photon Flux Density (PPFD)

PPFD, uitgedrukt in µmol m⁻² s

-1, meet het aantal fotosynthetisch actieve lichtfotonen dat een plantoppervlak bereikt. Dit is essentieel in vertical farming, waar kunstlicht de enige bron van energie is voor fotosynthese.

Sla en basilicum

- PPFD van 250 µmol m⁻² s
-1 is optimaal voor biomassa, kwaliteit en energiegebruik [2].
- 200 µmol m⁻² s
-1 volstaat bij hoge plantdichtheid (680 planten/m² ) [2].

Koriander

- PPFD van 250–300 µmol m⁻² s
-1 bevordert biomassatoename en antioxidantproductie [3].
- Optimale prestaties bij verhoogde worteltemperatuur en CO2 [3].

Aanbevolen richtlijn: Voor bladgewassen is 200–250 µmol m²
s

-1 geschikt, afhankelijk van ruimtegebruik en teeltstrategie.

### 5.1 PPFD-berekening

Voor een lade van 0.173 m² met 12 blauwe, 20 rode en 16 far-red LED’s geldt:

PPFtotaal = (12 × 1.01) + (20 × 0.76) + (16 × 0.72) = 12.12 + 14.4 + 11.52 = 38.04 µmol/s

PPFD = 38.84
0.173

= 224.50 µmol/m²
/s

Dit ligt binnen de aanbevolen zone (200–300 µmol/m²/s) voor bladgroenten. Dit zorgt voor optimale groei. [2, 3].

## 6 Afstand en uniformiteit

De LED’s worden op 25–30 cm boven het gewas geplaatst. Dankzij de brede uitstralingshoek (121–124°) ontstaat een egale belichting. De kast is voorzien van een witte coating die fungeert als reflectieve achtergrond en zo schaduwvorming vermindert.

## 7 Fotoperiode

Een cyclus van 16 uur licht en 8 uur donker (16L/8D) is toegepast, wat bewezen effectief is voor bladgroenten. [4].

## 8 Toepassingsgebied

### 8.1 PCB ontwerp

Voor het ontwerp van de PCB is er gekozen om eerder kleine PCB te maken om zo de lichtspreiding beter te kunnen managen. Er is een PCB bekomen zoals te zien is in fig:1


Figure 1: Opbouw van de LED-PCB

### 8.2 Uitvoering in de kast

De verlichting wordt toegepast in lades van 45,7 cm x 38 cm (0.174 m² ). Elke lade bevat
uiteindelijk 4 PCB’s met:
- 3 blauwe LED’s
- 5 rode LED’s
- 4 far-red LED’s

Totaal per lade: 12 blauwe, 20 rode, 16 far-reds.

## 9 Conclusie

De voorgestelde LED-configuratie voldoet aan de lichtbehoeften van bladgroenten in vertical farming. De gekozen PPFD-waarde en spectrumverhouding bevorderen vegetatieve groei met behoud van energie-effici¨entie en gelijkmatige belichting.

## References

[1] S. Zhen, M. Haidekker, and M. W. van Iersel, “Far-red light enhances photochemical efficiency in a wavelength-dependent manner,” Physiologia Plantarum, 2019.
[2] V. Jadhav, T. Grondona, A. Pistillo, G. Pennisi, M. Ghio, G. Gianquinto, and F. Orsini, “Optimizing planting density for increased resource use efficiency in baby-leaf production of lettuce (lactuca sativa l.) and basil (ocimum basilicum l.) in vertical farms,” ResearchGate, 2024.
[3] F. Wang, Q. Gao, G. Ji, J. Wang, Y. Ding, and S. Wang, “Effects of light intensity and photoperiod on morphological development and photosynthetic characteristics of coriander,” ResearchGate, 2024.
[4] S. D. Gupta, Light Emitting Diodes for Agriculture. Springer, 2017.

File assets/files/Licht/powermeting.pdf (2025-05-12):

# Ontwerp van een ZXCT1107 Stroommonitor

### Syme Vandenbosch

### 5 mei 2025

## 1 Inleiding

Om het vermogenverbruik van LED-lades nauwkeurig te meten, is een betrouwbare meting van de stroom naar de LED-PCB essentieel. Hiervoor is een sensor nodig die compatibel is met de analoge-naar-digitale converter (ADC) van de ESP32-microcontroller. De ZXCT1107, een high-side stroommonitor van Diodes Incorporated, is vergeleken met de ACS712 hallsensor en gekozen vanwege zijn hogere nauwkeurigheid bij stromen rond 2 A. Dit document beschrijft de keuze voor de ZXCT1107, vergelijkt beide sensoren en presenteert de berekeningen voor de weerstandswaarden om een sense-spanning van ongeveer 200 mV te bereiken, geschikt voor de ESP32.

## 2 Vergelijking van ZXCT1107 en ACS712

De ZXCT1107 is een shuntgebaseerde stroommonitor, terwijl de ACS712 een hallsensor gebruikt. Hieronder volgt een vergelijking van beide sensoren voor een toepassing met een stroom van 2 A.

### 2.1 ZXCT1107 (Shuntgebaseerd)

- Voordelen:

– Hoge nauwkeurigheid: Fout van ±2.8% bij VSENSE = 200 mV, ideaal voor stromen rond 2 A [1].

– Snelle respons: Bandbreedte van 0.65 MHz, geschikt voor dynamische metingen.

– Compact en kosteneffectief: SOT23-behuizing.

– Ongevoelig voor magnetische velden, zoals die van ventilatormotoren nabij de voeding.

- Nadelen:

– Vermogensverlies: De shuntweerstand veroorzaakt 0.4 W verlies bij 0.1 Ω en 2 A.

– Geen galvanische scheiding: Niet geschikt voor hoogspanning (niet nodig bij 24 V).

– Nauwkeurige weerstandskeuze vereist, wat de nauwkeurigheid bepaalt.

### 2.2 ACS712 (Hallsensor)

- Voordelen:

– Galvanische scheiding: Veilig bij hoogspanning, maar niet relevant bij 24 V [2].

– Eenvoudige integratie: Analoge uitgang compatibel met de ESP32 ADC.
– Geen spanningsval: Geen vermogensverlies in het stroompad.
- Nadelen:

– Lagere nauwkeurigheid: Resolutie van 100 mA, met meer ruis bij 2 A. – Langzamere respons: Niet geschikt voor snelle stroomveranderingen. – Gevoelig voor magnetische storingen, zoals van ventilatormotoren.

### 2.3 Reden voor de ZXCT1107

Voor een stroom van ongeveer 2 A biedt de ZXCT1107 een nauwkeurigere en stabielere meting dan de ACS712. De ESP32 ADC kan de uitgang direct verwerken, en galvanische scheiding is niet nodig bij een voeding van 24 V. De snelle respons en ongevoeligheid voor magnetische storingen, zoals veroorzaakt door ventilatormotoren nabij de voeding, maken de ZXCT1107 de meest geschikte keuze. Door toepassing van een lage shuntweerstand wordt het vermogensverlies geminimaliseerd.

## 3 Berekeningen voor Weerstandswaarden

Het circuit moet een stroom van 2 A meten met een sense-spanning van VSENSE ≈ 200 mV, en een uitgangsspanning leveren binnen het 0–3.3 V ADC-bereik van de ESP32. De ZXCT1107 heeft een transconductantie van 4 mA/V [1]:

IOUT = 0.004 · VSENSE (A).

De totale foutmarge is ±6%, rekening houdend met een apparaatfout van ±2.8% en weerstandstoleranties van ±1% per weerstand.

### 3.1 Shuntweerstand (RSENSE)

Voor VSENSE = 200 mV bij ILOAD = 2 A:

RSENSE =

VSENSE

ILOAD

=

0.2
2

= 0.1 Ω.

Een standaardweerstand van 0.1 Ω met 1% tolerantie wordt gekozen, wat een sense-spanning oplevert van:

VSENSE = ILOAD · RSENSE = 2 · 0.1 = 0.2 V = 200 mV.

### 3.2 Uitgangsstroom

De uitgangsstroom van de ZXCT1107 is:

IOUT = 0.004 · VSENSE = 0.004 · 0.2 = 0.0008 A = 800 µA.

### 3.3 Versterkingsweerstand (RGAIN)

Voor een uitgangsspanning van VOUT ≈ 2.5 V:

RGAIN =

VOUT

IOUT

=

2.5
0.0008

= 3125 Ω.

Een parallel schakeling van 3.3k en 33k in serie met een weerstand van 120 = 3120.

VOUT = IOUT · RGAIN = 0.0008 · 3120 = 2.568 V.

Dit ligt binnen het ADC-bereik van de ESP32.

### 3.4 Foutanalyse

De totale fout bestaat uit:

- Apparaatfout: ±2.8% [1].
- Weerstandstoleranties: ±5% per weerstand (voor RSENSE en RGAIN), totaal √ 5

2 + 5² =
±7.07%.

De gecombineerde fout is:

Totale fout = ±

q
(2.8%)² + (7.07%)² ≈ ±7.61%.

### 3.5 Vermogensdissipatie

- RSENSE:

PSENSE = I

2

LOAD · RSENSE = 2²
- 0.1 = 0.4W.

Een weerstand van 0.5 W wordt aanbevolen. Er is gekozen voor 2 x 0.25W parallel geplaatst.

- RGAIN:

PGAIN = I

2

OUT · RGAIN = (0.0008)²
- 3300 = 0.002112 W = 2.112 mW.

Een standaardweerstand van 0.25 W volstaat.

## 4 Conclusie

Met RSENSE = 0.1 Ω en RGAIN = 3120 kΩ levert de ZXCT1107 een sense-spanning van VSENSE = 200 mV en een uitgangsspanning van VOUT = 2.56 V, met een totale fout van ±28.41%. Dit maakt het circuit geschikt voor nauwkeurige meting van een 2 A LEDstroom met de ESP32. Het schema, inclusief een buckconverter voor de 3.3 V voeding van de driver-PCB, is opgenomen in de appendix.

## Referenties

[1] Diodes Incorporated, ZXCT1107/ZXCT1109 Low Power Current Monitors, Datasheet, 2010. Beschikbaar via: https://www.diodes.com/datasheet/download/ZXCT1107.pdf. (https://www.diodes.com/datasheet/download/ZXCT1107.pdf)
[2] Allegro MicroSystems, ACS712 Fully Integrated, Hall Effect-Based Linear Current Sensor IC, Datasheet, 2020. Beschikbaar via: https://www.allegromicro.com/-/media/files/datasheets/acs712-datasheet.ashx. (https://www.allegromicro.com/-/media/files/datasheets/acs712-datasheet.ashx)

## Appendix

Hieronder is het schema van het stroommeetcircuit met de ZXCT1107 opgenomen.


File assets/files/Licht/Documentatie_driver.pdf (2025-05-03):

# Documentatie driver

## inleiding

Voor de aansturing van de LEDs maken we gebruik van de AL1793AFE-13 driver. Deze driver beschikt over drie afzonderlijk aanstuurbare kanalen, die elk via PWM-signalen geregeld kunnen worden. Daarnaast biedt de driver foutdetectie en beveiliging tegen oververhitting en defecte LED-componenten.

## ESP32 Basiscomponenten

De ESP32 vereist een aantal essentiële componenten voor een correcte werking (zie figuur 1). Dit omvat onder andere ontkoppelcondensatoren en een opstartcircuit. Daarnaast wordt een LDO-regelaar gebruikt om de 24 VDC voedingsspanning om te zetten naar 3,3 VDC, wat noodzakelijk is voor de werking van de ESP32.
Voor de programmering van de ESP32 zijn aansluitingen voorzien voor TX, RX, GND en 3,3 V.


Figuur 1: esp-wroon
De voedingsspanning van de driver (figuur 2) bedraagt 24 V. Om de stroom door de LEDs nauwkeurig te regelen, wordt een weerstand aangesloten op de REF-pin. De waarde van deze weerstand wordt berekend met de volgende formule (de gewenste stroom is 140 mA voor de LEDs):

ILEDX = 2000

VREF

RSET

= 2000

1,5

RSET

RSET = 2000

1,5
0,140 = 21428,57 Ω

Voor een gewenste LED-stroom van 140 mA wordt de weerstandswaarde benaderd door twee parallelle weerstanden te combineren:
- R6 = 22 kΩ
- R7 = 1MΩ.

Controle:

22000 . 1000000
22000 + 1000000 = 21526,42 Ω

Weerstanden R3, R4 en R5 zijn opgenomen in het circuit om eventuele overtollige spanning te absorberen en zo de stabiliteit van de schakeling te waarborgen. De LEDPG- en FAULT-pinnen van de driver geven foutmeldingen weer. Deze pinnen vereisen een pull-up weerstand om correct te functioneren.


Figuur 2: AL1793AFE-13 driver

## Aansturing via ESP32

Een enkele ESP32 stuurt in totaal drie drivers (figuur 3) aan. Elke driver maakt gebruik van de volgende pinnen:
- Enable (EN)
- Drie PWM-kanalen (PWM1 - PWM3)
- LEDPG en FAULT voor foutdetectie


Figuur 3: ESP32 & drivers

Hierdoor zijn in totaal 18 pinnen van de ESP32 nodig om de drie drivers correct aan te sluiten:

esp 32 | driver
| driver 1
IO21 | EN
IO5 | PWM1
IO18 | PWM2
IO19 | PWM3
IO23 | LEDPG
IO22 | FAULT
| driver 2
IO17 | EN
IO12 | PWM1
IO13 | PWM2
IO15 | PWM3
IO4 | LEDPG
IO16 | FAULT
| driver 3
IO26 | EN
IO32 | PWM1
IO33 | PWM2
IO25 | PWM3
IO27 | LEDPG
IO14 | FAULT

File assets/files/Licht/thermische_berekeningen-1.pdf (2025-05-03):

# Thermische Berekeningen

Syme Vandenbosch

februari 2025

## Inleiding

In dit document worden de thermische berekeningen besproken die gemaakt zijn voor de led-PCB met betrekking tot de vertical farm. Het doel van deze berekeningen is om na te gaan of de warmte die gedissipeerd wordt door de leds, op een effici¨ente manier kan afgevoerd worden. Hierbij wordt er gekeken naar de thermische weerstand van verschillende onderdelen, via’s, PCB, en de koelplaat. Aan de hand van deze gegevens kan bepaald worden of extra maatregelen zoals actieve of passieve koeling nodig zijn om de levensduur van de led te verlengen.

## 1 Thermische Berekeningen

In deze sectie wordt dieper ingegaan op de nodige berekeningen en de aspecten die belangrijk zijn voor de thermische vereisten van de leds. Er wordt dieper ingegaan op de bijkomende aspecten bij het ontwerp van een led-PCB.

### 1.1 Berekening van de via’s

Via de applicatie https://circuitcalculator.com/wordpress/2006/03/12/pcb-via-calculator/.


Figure 1: Berekening van de thermische weerstand van de via

De thermische weerstand van ´e´en via bedraagt 90.9 °C/W. Er is zo een goed mogelijke warmteafvoer gewenst. Daarom is er gekozen om zoveel mogelijk via’s te plaatsen voor een goed warmteafvoer te kunnen garanderen. Echter wordt er bij de verdere thermische berkeningen slechts gerekend met tien via’s aan elke zijde van de led.

Wat resulteert in een totaal van 20 via’s. De rede hiervoor is dat deze 20 via’s dicht genoeg bij de led staan om een aanzienelijk aandeel te hebben bij de warmte afvoer. De extra’s zijn toegevoegd om wat marge te hebben.

De thermische weerstand van ´e´en via bedraagt:

Rth via-copper =

Rth tot

nvia’s

=

90.9
20
= 4.55 ◦C/W | (1)

Hierbij is:

Rth via-copper = de thermische weerstand van via naar het koper (25°C)

Rth tot = totale waarde van de thermische weerstand van de via nvia’s = het aantal via’s

### 1.2 Berekening van de PCB

FR-4 is een van de meest gebruikte printplaatmaterialen en is een met glasvezel versterkte epoxyhars. Het heeft een lage thermische geleidbaarheid, wat betekent dat warmte niet gemakkelijk door het materiaal stroomt. Dit maakt thermisch beheer in PCB-ontwerpen een belangrijke factor. Om de thermische weerstand zo laag mogelijk te houden, is ervoor gekozen om de PCB een dikte te geven van 0.8mm i.p.v. de normale standaard dikte van 1.6mm. De PCB heeft dus een opbouw zoals weergegeven wordt in fig:2 [1] [2]

Figure 2: Doorsnede van een eenlaag FR-4 PCB [2]

De thermische weerstand van de PCB wordt berekend met de volgende formule:

θ =

l
k · A

(2)

waarbij:

- l = 0.0008 m (dikte van de PCB),
- A = 225 × 10⁻⁶ m² (warmteafvoeroppervlak),
- k = 0.2 W/mK (thermische geleidbaarheid van FR-4).

Invullen in de formule geeft:

θ =

0.0008
0.2 × 225 × 10⁻⁶

=

0.0008
0.000045
= 17.78 °C/W | (3)
Laag/Materiaal | Dikte (µm) | Thermische geleidbaarheid (W/mK)
SnAgCu soldeer Toplaag koper FR-4 di¨elektricum | 75 70 802 | 58 398 0.2

Table 1: Typische thermische geleidbaarheden van FR-4 PCB-lagen [2]

De themische weerstand van de PCB bedraagt dus 17,78 °C/W. Er wordt best nog wat marge ingerekend dus er zal verder gerekend worden met een waarde van 40 °C/W. Dit lijkt ruim gerekend maar dit kan eventuele afwijkingen van die bij de berekeningen van de via’s bekomen zijn te compenseren.

### 1.3 Berekening van de led

De led temperatuur is afhankelijk van verschillende factoren en wordt opgesplitst in:

Rth j-solder, Rth solder-via, Rth via-copper, Rth copper-ambient

Hierbij is:

Rth j-solder = de thermische weerstand van de junctie naar de soldeerverbinding Rth solder-via = de thermische weerstand van de soldeerverbinding naar de via’s Rth via-copper = de thermische weerstand van de via’s naar het koelvlak
Rth copper-ambient = de thermische weerstand van het koelvlak naar de omgeving

De bijhorende waarden voor deze thermische weerstanden kunnen worden afgelezen in:

Benaming | Waarde (°C/W) | Verklaring van de waarde
Rth j-solder Rth solder-via Rth via-copper Rth copper-ambient | 15 3 4,55 40 | Dit wordt weergegeven in de datasheet (far red is hoogste) Dit is een algemene waarde Dit is berekend in 1.1 Berekend in punt 1.2 + marge

Table 2: Thermische weerstandswaarden zonder koeling

De thermische weerstand van de led bedraagt:

Rth led = (Rth j-solder + Rth solder-via + Rth via-copper + Rth copper-ambient)

Rth led = 15◦C/W + 3◦C/W + 4, 55◦C/W + 40◦C/W = 62, 55◦C/W

∆Tled = Rth led · Pled = 62, 55◦C/W · (240mA × 3V ) = 45, 036◦C

Tjunctie = Tomegving + ∆Tled = 25◦C + 45, 036◦C = 70, 036◦C

In de datasheet van de Cree leds staat dat de maximale junctie temperatuur 125◦C mag bedragen. De berekende waarde is dus lager dan de maximale waarde. Dit betekent dat de led niet oververhit zal raken. Om de levensduur te bevorderen, wordt aangeraden om de leds passief of actief te koelen. Dit zal de levensduur aanzienelijk verlengen. [3]

### 1.4 Berekening van de koelplaat

Om de levensduur van de leds te kunnen verlengen wordt er gekozen om de leds te laten werken op een maximale temperatuur van 45◦C. Er zal dus een koelplaat nodig zijn voor de nodige thermische afvoer. Men bekomt dan een opbouw zoals in weergegeven wordt in fig:3 [1] [2]


Figure 3: Doorsnede van een eenlaag FR-4 PCB [2]

De bijhorende waarden voor deze thermische weerstanden kunnen worden afgelezen in:

Benaming | Waarde (°C/W) | Verklaring van de waarde
Rth j-solder Rth solder-via Rth via-coolpad Rth coolpad-heatsink Rth heatsink-ambient | 15 3 4,55 7 0.29 | Dit wordt weergegeven in de datasheet (far red is hoogste) Dit is een algemene waarde Berekend in punt 1.1 Uit de datasheet Uit de datasheet

Table 3: Thermische weerstandswaarden met koeling

De thermische weerstand van de totale PCB bedraagt:

Rth pcb = (Rth j-solder + Rth solder-via + Rth via-coolpad + Rth coolpad-heatsink + Rth heatsink-ambient)

Rth pcb = 15◦C/W + 3◦C/W + 4, 55◦C/W + 7◦C/W + 0, 29◦C/W = 29, 84◦C/W

∆Tled = Rth pcb · Pled = 29, 84◦C/W · (240mA × 3V ) = 21, 49◦C

Tjunctie = Tomgeving + ∆Tled = 25◦C + 21, 49◦C = 46, 49◦C

De Led zullen dan op een temperatuur van 46,49°C functioneren. Dit is in de grootorde van de gewenste temperatuur voor de leds.

## Conclusie

Uit de berekeningen blijkt dat de totale thermische weerstand zonder koeling vrij hoog is, wat resulteert in een junctietemperatuur van net boven de 70°C. Dit is wel onder de maximaal toegelaten waarde van 125°C die weergegeven wordt in de datasheet, maar om de betrouwbaarheid en levensduur van de LED te verbeteren is extra koeling aangewezen. Door toevoeging van een koelplaat wordt de junctietemperatuur verlaagd tot ongeveer 46°C, wat zorgt voor een veilige marge. Zo zal de led aanzienlijk langer kunnen functioneren zonder door te branden.

## References

[1] Texas Instruments. Thermal management guide. Technical Report SLPA015, 2006.
[2] CREE LEDs. Optimizing pcb thermal performance for xlamp. Technical report, 2010-2023.
[3] CREE LEDs. J series 2835 color leds, 2023-2024.

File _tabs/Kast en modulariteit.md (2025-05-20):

---
icon: fas fa-screwdriver-wrench
order: 6       
---

## Inhoud 
1. [Binnen- en buitenkast](#binnen--en-buitenkast)
2. [Modulariteit](#modulariteit)

## Binnen- en buitenkast
De kast bestaat uit twee grote delen, een binnenkast en een buitenkast. Ze is ontworpen met voorradige materialen, grotendeels gerecupereerd uit het project van afgelopen jaar. De binnenkast huist de elektronica en de lades. De buitenkast trekt de binnenkast in plaats en zorgt voor een mooie afwerking van het geheel. De buitenkast kan aan de hand van enkele bouten losgemaakt worden van de binnenkast, dit is ideaal voor onderhoud of het verplaatsen van de kast. De gebruikte onderdelen zijn ook te vinden in de BOM.

De plannen voor de buitenkast kunt u hier bekijken:
<a href="https://github.com/Vertical-Farming-IB3/Plan-T/blob/main/Kast/vertical_farming_250425.pdf" target="_blank">📄 Technische tekeningen</a>

Buitenkast concept

## Modulariteit
Een belangrijk aspect waarmee we rekening hebben gehouden tijdens het ontwerpen van de vertical farm is de modulariteit. Dit slaat zowel op de mogelijkheid de kast te personaliseren aan verschillende noden als op de mogelijkheid om de kast (makkelijk) te verplaatsen en te onderhouden. Bij de opdracht van een vertical farm voor een huishoudelijke setting dachten we aan een kast. De vertical farm is dan ook gebaseerd op een (koel)kastontwerp. Er is hierbij een vast deel elektronica en schappen (lades) in de kast die naar persoonlijke voorkeur ingericht kunnen worden.
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

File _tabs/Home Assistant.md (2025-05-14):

---
title: "Home Assistant"
icon: fas fa-house-signal
order: 5
layout: default
---

## Inhoud 
1. [Dashboard](#dashboard)
  - [Home](#home)
  - [Lades](#lades)
  - [Energieverbruik](#energieverbruik)
  - [Watersysteem](#watersysteem)
2. [Data aggregatie](#data-aggregatie)
3. [Automatisaties](#automatisaties)
4. [Wachtwoorden](#wachtwoorden)

# Dashboard

Bij onze slimme vertical farm hoort natuurlijk ook een interactief dashboard waar ook alle data wordt verzameld. 

Wanneer u surft naar het Home Assistant dashboard <em>(http://homeassistant.local:8123)</em> of de Home Assistant app opent vindt u verschillende dashboards terug. Eventueel heeft u een wachtwoord nodig om in te loggen, deze wachtwoorden staan [hier](#wachtwoorden) opgesomd. U klikt links op 'Home' voor de toegang tot de hieronder besproken dashboards.
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

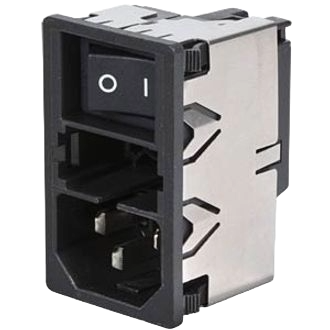
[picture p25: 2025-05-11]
assets/img/Licht/main connector.png

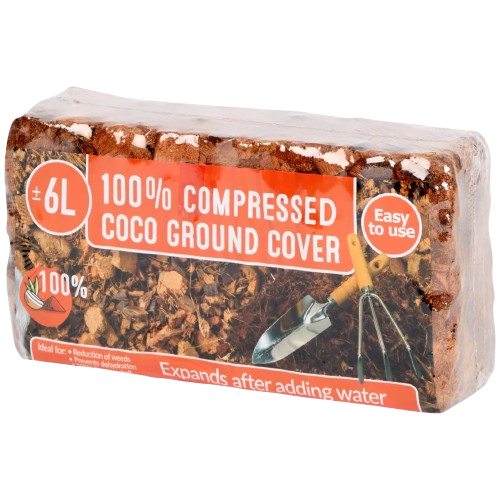
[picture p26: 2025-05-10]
assets/img/Plantenbak/kokosvezel.png

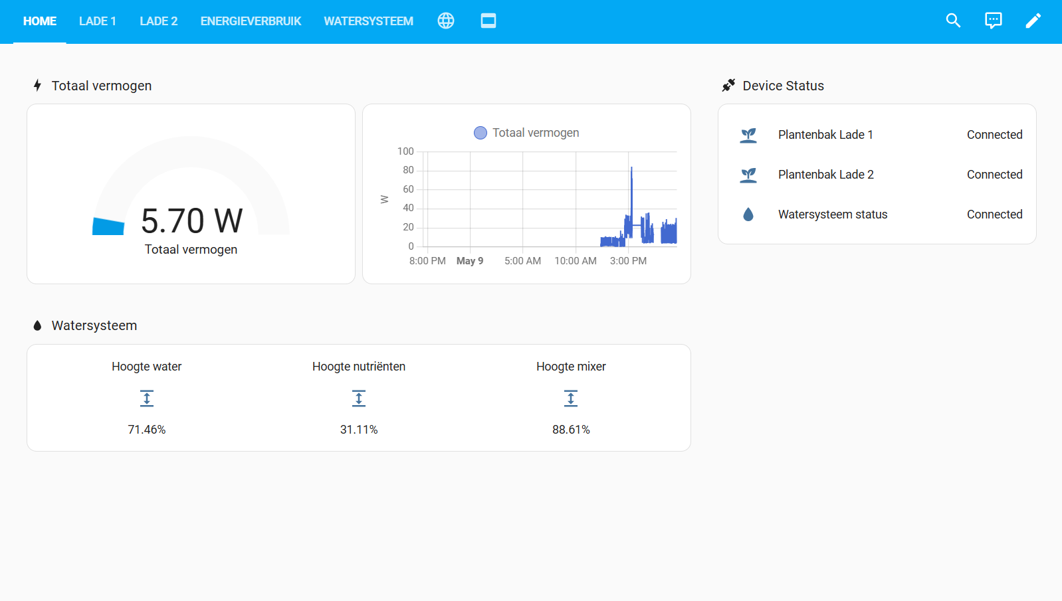
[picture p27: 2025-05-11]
assets/img/HomeAssistant/Home.png

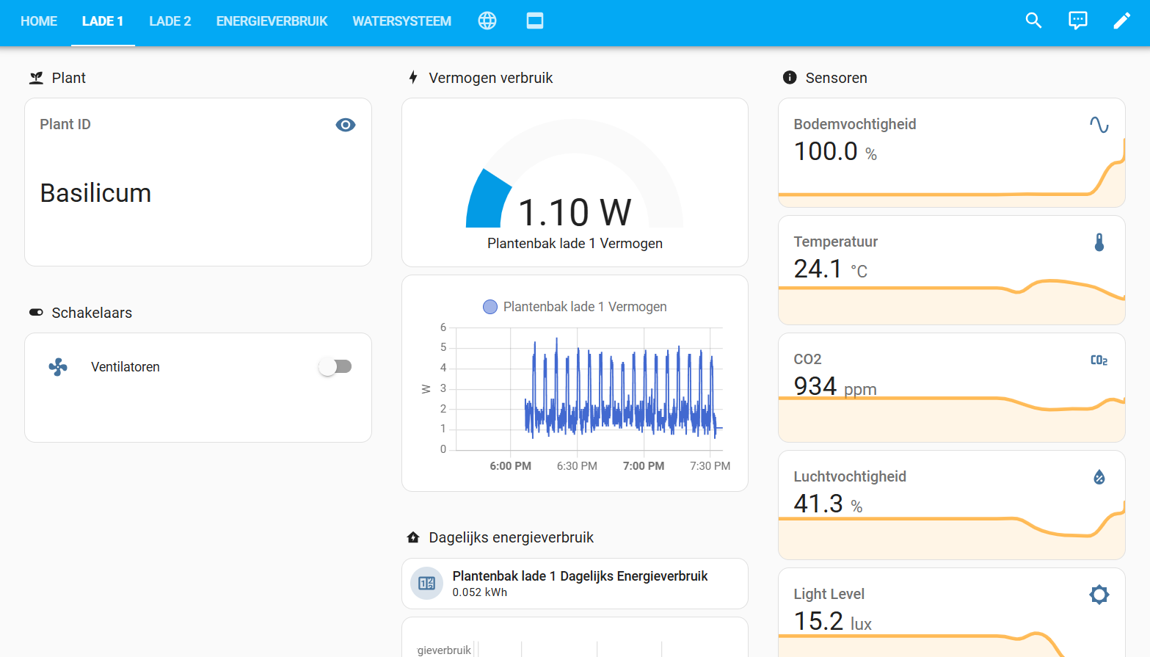
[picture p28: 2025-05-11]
assets/img/HomeAssistant/Lade_1.png

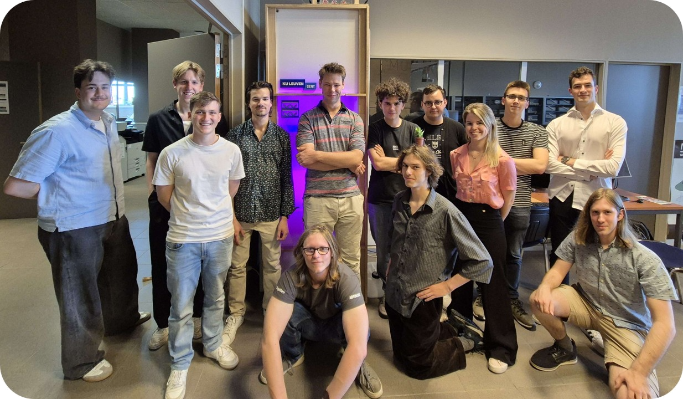
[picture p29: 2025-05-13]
assets/img/Home/Team.png

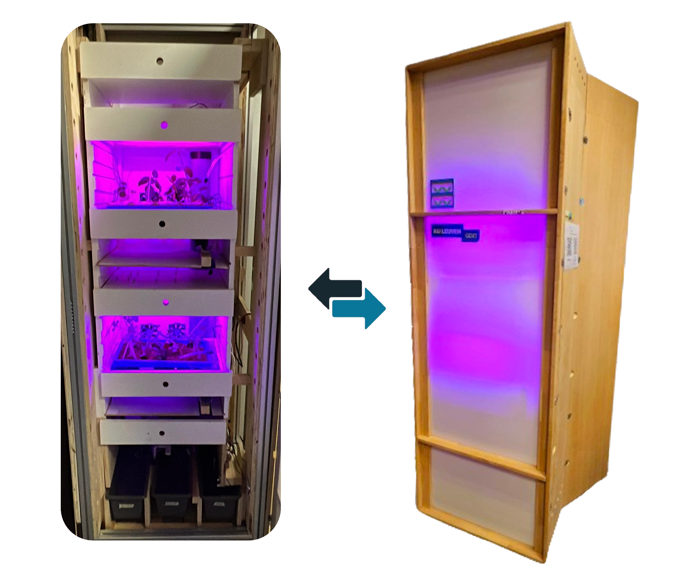
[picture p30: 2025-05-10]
assets/img/Home/kast.png

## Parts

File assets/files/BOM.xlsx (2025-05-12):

Component | Status | Link | Aantal/module plantenbak | Aantal/module kast | Aantal in bezit | Totaal aantal | Totaal aantal te bestellen | Prijs/eenheid | Kost | Prijs | Info | Totaal Watersysteem (Te bestellen) | Aantal modules kast:
WATERSYSTEEM |  |  |  |  |  |  |  |  |  |  |  | €123.39 | 1
Waterpomp (12VDC) | In bezit | TinyTronics (https://www.tinytronics.nl/nl/mechanica-en-actuatoren/motoren/pompen/waterpomp-12v) |  | 4 |  | 4 | 4 | €6.00 | €24.00 | €24.00 |  |  | Aantal modules plantenbak per module kast:
Aquariumpomp (mengen) | In bezit | TinyTronics (https://www.tinytronics.nl/nl/mechanica-en-actuatoren/motoren/pompen/onderwaterpomp-horizontaal-3-6v) |  | 1 |  | 1 | 1 | €4.00 | €4.00 | €4.00 |  |  | 2
Sensor ISE-2922 NO3- | In bezit | MTLAB (http://www.measureteq.com/electrode-and-sensor/ion-selective-electrode/ise-2922-no3-nitrate-ion-selective-electrode.html) |  | 1 | 1 | 1 | 0 | €36.83 | €36.83 | €0.00 |  |  | Totaal aantal modules plantenbak:
Sensor ISE-2923 Ca2+ | In bezit | MTLAB (http://www.measureteq.com/electrode-and-sensor/ion-selective-electrode/ise-2923-calcium-ion-selective-electrode-ise.html) |  | 1 | 1 | 1 | 0 | €27.62 | €27.62 | €0.00 |  |  | 2
Sensor ISE-2920 K+ | In bezit | MTLAB (http://www.measureteq.com/electrode-and-sensor/ion-selective-electrode/ise-2920-potassium-ion-selective-electrode.html) |  | 1 | 1 | 1 | 0 | €32.22 | €32.22 | €0.00
ADC | In bezit |  |  | 1 | 1 | 1 | 0 | €0.00 | €0.00 | €0.00 | op pcb
UV | Kapot | Aliexpress (https://nl.aliexpress.com/item/1005004493335123.html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) |  | 1 |  | 1 | 1 | €10.43 | €10.43 | €10.43 |  |  | TOTAAL TE BESTELLEN: | Excl verzending, excl xtra kosten, incl btw
Waterhoogte sensor: Ultrasoon | In bezit | TinyTronics (https://www.tinytronics.nl/nl/sensoren/afstand/ultrasonische-afstandssensor-rcwl-1604) |  | 3 | 3 | 3 | 0 | €2.75 | €8.25 | €0.00 |  |  | €766.62
QuickConnect | In bezit | Aliexpress (https://nl.aliexpress.com/item/1005005808872752.html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) | 2 | 4 |  | 4 | 1 | €0.97 | €3.88 | €0.97 | PU-8 voor 8 mm OD (1x 10 stuks bestellen)
Waterslang (6mm ID-8mm OD) | In bezit | TinyTronics (https://www.tinytronics.nl/nl/mechanica-en-actuatoren/onderdelen/slangen/waterslang-voor-onderwaterpomp-verticaal-horizontaal-3-6v-transparant-1-meter) |  | 6 |  | 6 | 6 | €1.50 | €9.00 | €9.00 | per meter (AAN 1 STUK BESTELLEN!)
Silicone kit | In bezit | Hubo (https://www.hubo.be/nl/p/hubo-siliconenkit-sanitair-310ml-transparant/12507/) |  | 1 | 1 | 1 | 0 | €6.50 | €6.50 | €0.00
Klemringen/Slangklemmen | In bezit | Aliexpress (https://nl.aliexpress.com/item/1005007403359089.html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) |  | 1 |  | 1 | 1 | €2.33 | €2.33 | €2.33 | Per 10
Reservoir | In bezit | Vorig jaar |  | 4 | 4 | 4 | 0 | €2.99 | €11.96 | €0.00
Luchtsteen | In bezit | Aliexpress (https://nl.aliexpress.com/item/1005007443597285.html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) |  | 2 |  | 2 | 2 | €0.97 | €1.94 | €1.94
T-stuk (luchtsteen) | In bezit | Aliexpress (https://nl.aliexpress.com/item/32900110036.html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) |  | 1 |  | 1 | 1 | €0.97 | €0.97 | €0.97
Luchtpomp | In bezit | TinyTronics (https://www.tinytronics.nl/nl/mechanica-en-actuatoren/motoren/pompen/luchtpomp-pyp370-12z-12v) |  | 2 |  | 2 | 2 | €4.50 | €9.00 | €9.00
Waterslang (3.5mm ID-Xmm OD) | In bezit | TinyTronics (https://www.tinytronics.nl/nl/mechanica-en-actuatoren/onderdelen/slangen/lucht-water-slang-3.5mm-transparant-1m) |  | 1 |  | 1 | 1 | €2.00 | €2.00 | €2.00 | per meter, 3.5mm
Eindloopschakelaar | In bezit | Hobbyelectronica (https://www.hobbyelectronica.nl/product/3d-printer-endstop-mechanisch-ramps-1-4/) |  | 3 | 3 | 3 | 0 | €1.95 | €5.85 | €0.00
PCB | In bezit | PCBWay (https://www.pcbway.com/) |  | 1 |  | 1 | 1 | €4.39 | €4.39 | €4.39
Relais 5V | In bezit | Mouser (https://www.mouser.be/ProductDetail/Amphenol-Anytek/AHQSS105DM2FA0G) |  | 10 |  | 10 | 10 | €1.47 | €14.70 | €14.70
Waterslang | In bezit | tinytronics (https://www.tinytronics.nl/nl/mechanica-en-actuatoren/onderdelen/slangen/waterslang-voor-onderwaterpomp-verticaal-horizontaal-3-6v-transparant-1-meter) |  | 1 |  | 1 | 1 | €1.50 | €1.50 | €1.50
PPF | In bezit | AliExpress (https://nl.aliexpress.com/item/1005008183056175.html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) |  | 5 |  | 5 | 5 | €0.75 | €3.80 | €3.80
PH- sensor + ADC | In bezit | AliExpress (https://nl.aliexpress.com/item/1005006063176996.html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) |  | 1 |  |  | 1 | €4.52 | €4.52 | €4.52
UV-C filter (nieuw) [14W - ordinary] | In bezit | AliExpress (https://nl.aliexpress.com/item/1005006110975582.html?scm_id=1007.40050.354490.0&scm-url=1007.40050.354490.0) |  | 1 |  |  | 1 | €29.84 | €29.84 | €29.84
Componenten PCB
Footprint | Value | References |  |  |  |  |  |  |  |  | Aanwezig op campus
C_0805_2012Metric_Pad1.18x1.45mm_HandSolder | 100n | C3, C4, C6, C7, C10, C11, C12, C13, C14 |  | 9 | 9 | 9 | 0 | - | - | -
CP_Elec_6.3x3.9 | 100u | C1, C2 |  | 2 | 2 | 2 | 0 | - | - | -
C_0805_2012Metric_Pad1.18x1.45mm_HandSolder | 10u | C5, C9 |  | 2 | 2 | 2 | 0 | - | - | -
CP_EIA-3528-12_Kemet-T_Pad1.50x2.35mm_HandSolder | 22u | C8 |  | 1 | yyyyy | 1 | 0 | - | - | -
R_0805_2012Metric_Pad1.20x1.40mm_HandSolder | 10k | R2, R4, R5, R6, R7, R8, R9, R11, R13 |  | 9 | 9 | 9 | 0 | - | - | -
R_0805_2012Metric_Pad1.20x1.40mm_HandSolder | 470 | R1, R3, R14, R15 |  | 4 | 4 | 4 | 0 | - | - | -
R_0805_2012Metric_Pad1.20x1.40mm_HandSolder | 4.7k | R10, R12 |  | 2 | 2 | 2 | 0 | - | - | -
D_0805_2012Metric_Pad1.15x1.40mm_HandSolder | 1N4148 | D4, D5, D6, D7, D8, D9, D10 |  | 7 | 7 | 7 | 0 | - | - | -
LED_0805_2012Metric_Pad1.15x1.40mm_HandSolder | PWR | D1 |  | 1 | 1 | 1 | 0 | - | - | -
LED_0805_2012Metric_Pad1.15x1.40mm_HandSolder | LED | D2 |  | 1 | 1 | 1 | 0 | - | - | -
DIOM5226X290N | SK36A | D3 |  | 1 | 1 | 1 | 0 | - | - | -
MP1584_Module | MP1584_Module | U1 |  | 1 | 1 | 1 | 0 | - | - | -
ESP32-WROOM-32D | ESP32-WROOM-32D | U2 |  | 1 | 1 | 1 | 0 | - | - | -
TSSOP-10_3x3mm_P0.5mm | ADS1115IDGS | U3 |  | 1 | 1 | 1 | 0 | - | - | -
SOT-223-3_TabPin2 | AMS1117-3.3 | U4 |  | 1 | 1 | 1 | 0 | - | - | -
SOIC-28W_7.5x17.9mm_P1.27mm | MCP23017_SO | U5 |  | 1 | 1 | 1 | 0 | - | - | -
Wurth_Tactile_Switch_SPST-NO_434111043826 | EN | SW1 |  | 1 | 1 | 1 | 0 | - | - | -
Wurth_Tactile_Switch_SPST-NO_434111043826 | BOOT | SW2 |  | 1 | 1 | 1 | 0 | - | - | -
AHQSS105DM2FA0G | AHQSS105DM2FA0G | K1, K2, K3, K4, K5, K6, K7 |  | 7 | 7 | 7 | 0 | - | - | -
SOT-23 | BSS138 | Q1, Q2, Q3, Q4, Q5, Q6, Q7 |  | 7 | 7 | 7 | 0 | - | - | -
MountingHole_3.2mm_M3_Pad_TopBottom | MountingHole_Pad | H1, H2, H3, H4 |  | 4 | 4 | 4 | 0 | - | - | -
SolderJumper-2_P1.3mm_Open_RoundedPad1.0x1.5mm | SolderJumper_2_Open | JP1, JP2, JP3, JP4 |  | 4 | 4 | 4 | 0 | - | - | -
TestPoint_Pad_D2.0mm | TestPoint | TP1, TP2, TP3, TP4 |  | 4 | 4 | 4 | 0 | - | - | -
PinHeader_1x04_P2.54mm_Vertical | Height Water | J1 |  | 1 | 1 | 1 | 0 | - | - | -
PinHeader_1x04_P2.54mm_Vertical | Height Nutrients | J2 |  | 1 | 1 | 1 | 0 | - | - | -
PinHeader_1x04_P2.54mm_Vertical | Height Mixer | J3 |  | 1 | 1 | 1 | 0 | - | - | -
PinHeader_1x02_P2.54mm_Vertical | TestPins | J4 |  | 1 | 1 | 1 | 0 | - | - | -
TerminalBlock_Phoenix_PT-1,5-2-5.0-H_1x02_P5.00mm_Horizontal | 12V ingang | J5 |  | 1 | 1 | 1 | 0 | - | - | -
TerminalBlock_Phoenix_PT-1,5-2-5.0-H_1x02_P5.00mm_Horizontal | Pomp1 | J6 |  | 1 | 1 | 1 | 0 | - | - | -
PinHeader_1x04_P2.54mm_Vertical | TTL Connector | J7 |  | 1 | 1 | 1 | 0 | - | - | -
PinHeader_1x03_P2.54mm_Vertical | Endstop UV | J8 |  | 1 | 1 | 1 | 0 | - | - | -
PinHeader_1x03_P2.54mm_Vertical | Endstop Lade1 | J9 |  | 1 | 1 | 1 | 0 | - | - | -
BNC_Amphenol_B6252HB-NPP3G-50_Horizontal | ReferentieProbe | J10 |  | 1 | 1 | 1 | 0 | - | - | -
PinHeader_1x03_P2.54mm_Vertical | Endstop Lade0 | J11 |  | 1 | 1 | 1 | 0 | - | - | -
TerminalBlock_Phoenix_PT-1,5-2-5.0-H_1x02_P5.00mm_Horizontal | Pomp2 | J12 |  | 1 | 1 | 1 | 0 | - | - | -
PinHeader_1x02_P2.54mm_Vertical | LED Water Level | J13 |  | 1 | 1 | 1 | 0 | - | - | -
PinHeader_1x02_P2.54mm_Vertical | LED Nutrient Level | J14 |  | 1 | 1 | 1 | 0 | - | - | -
BNC_Amphenol_B6252HB-NPP3G-50_Horizontal | Voedingsstoffen 1 | J15 |  | 1 | 1 | 1 | 0 | - | - | -
TerminalBlock_Phoenix_PT-1,5-2-5.0-H_1x02_P5.00mm_Horizontal | Pomp3 | J16 |  | 1 | 1 | 1 | 0 | - | - | -
TerminalBlock_Phoenix_PT-1,5-2-5.0-H_1x02_P5.00mm_Horizontal | Pomp4 | J17 |  | 1 | 1 | 1 | 0 | - | - | -
PinHeader_1x06_P2.54mm_Vertical | Backup GPIO | J18 |  | 1 | 1 | 1 | 0 | - | - | -
BNC_Amphenol_B6252HB-NPP3G-50_Horizontal | Voedingsstoffen 2 | J19 |  | 1 | 1 | 1 | 0 | - | - | -
TerminalBlock_Phoenix_PT-1,5-2-5.0-H_1x02_P5.00mm_Horizontal | Luchtpomp | J20 |  | 1 | 1 | 1 | 0 | - | - | -
BNC_Amphenol_B6252HB-NPP3G-50_Horizontal | Voedingsstoffen 3 | J21 |  | 1 | 1 | 1 | 0 | - | - | -
TerminalBlock_Phoenix_PT-1,5-2-5.0-H_1x02_P5.00mm_Horizontal | Mixer | J22 |  | 1 | 1 | 1 | 0 | - | - | -
TerminalBlock_Phoenix_PT-1,5-2-5.0-H_1x02_P5.00mm_Horizontal | 230V | J23 |  | 1 | 1 | 1 | 0 | - | - | -
TerminalBlock_Phoenix_PT-1,5-2-5.0-H_1x02_P5.00mm_Horizontal | UV | J24 |  | 1 | 1 | 1 | 0 | - | - | -
PLANTENBAK |  |  |  |  |  |  |  |  |  |  |  | Totaal Plantenbak (Te bestellen)
Capacitive soil moisture sensor | In bezit |  | 1 | 2 | 2 | 2 |  |  |  |  |  | €87.43
GY-SCD40 module | In bezit |  | 1 | 2 | 2 | 2
NFC-reader PN532 | In bezit |  | 1 | 2 | 2 | 2
NFC-tags | In bezit |  | 1 | 2 | 2 | 2
Nieuwe PCB's | In bezit | PCBWay (https://www.pcbway.com/) | 1 | 2 |  | 2 | 2 |  |  | €4.39
BH1750 lichtsensor | In bezit | Hobbyelectronica (https://www.hobbyelectronica.nl/product/bh1750-digitale-licht-sensor/) | 1 | 2 |  | 2 | 2 | €2.25 | €4.50 | €4.50
CH340C | In bezit | AliExpress (https://www.aliexpress.com/item/1005006040438712.html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) | 1 | 2 |  | 10 | 10 | €0.41 | €4.05 | €4.05
ESP-WROOM-32 | In bezit
Ventilatoren (12V) | In bezit |  | 2 | 4 |  | 4 | 4
Relais SR5 | In bezit | Digikey (https://www.digikey.be/en/products/detail/same-sky-formerly-cui-devices/SR5-3V-200-1C/16602081) | 1 | 2 |  | 2 | 2 | €1.13 | €2.26 | €2.26
MP1584 | In bezit | TinyTronics (https://www.tinytronics.nl/en/power/voltage-converters/buck-(step-down)-converters/mini-dc-dc-adjustable-step-down-buck-converter-1a-mp1584) | 1 | 2 |  | 2 | 2 | €1.50 | €3.00 | €3.00
Dupont kabels | In bezit |  |  |  |  | 4 | 4 | €2.00 | €8.00 | €8.00
5V relais | In bezit | Tinytronics (https://www.tinytronics.nl/nl/schakelaars/relais/relais-modules/5v-relais-1-channel-hoog-actief-of-laag-actief) |  |  |  | 2 | 2 | €2.50 | €5.00 | €5.00
Rockwool aliexpress | In bezit | AliExpress (https://www.aliexpress.com/item/1005007321849079.html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) |  |  |  | 1 | 1 | €4.65 | €4.65 | €4.65 | 100 stuks per batch
Potjes voor plantjes: NO.40 white | In bezit | AliExpress (https://nl.aliexpress.com/item/1005004666016798.html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) |  |  |  | 2 | 2 | €3.28 | €3.28 | €6.56 | NO.50 white (15 stuk per batch)
Witte verf | In bezit | Action (https://www.action.com/nl-be/p/3015431/spectrum-2-in-1-hoogglans-verf-wit/) |  |  |  | 1 | 1 | €7.99 | €7.99 | €7.99
Verfborstel en verfbak | In bezit | action |  |  |  | 1 | 1 | €1.84 | €1.84 | €1.84
Kokosvezel potgrond | In bezit | Action (https://www.action.com/nl-be/p/2520586/kokos-potgrond/) |  |  |  | 3 | 3 | €1.17 | €3.51 | €3.51
Plantenvoeding | In bezit | Action (https://www.action.com/nl-be/p/3004917/green-boots-biologische-plantenvoeding-voor-groenten/) |  |  |  | 2 | 2 | €1.79 | €3.58 | €3.58
Bloempotjes | In bezit | action |  |  |  | 2 | 2 | €1.11 | €2.22 | €2.22
Hydrokorrels | In bezit | Action (https://www.action.com/nl-be/p/2562268/hydrokorrels/) |  |  |  | 1 | 1 | €2.37 | €2.37 | €2.37
Glasbokalen | In bezit | Action (https://www.action.com/nl-be/p/2552569/voorraadpot/) |  |  |  | 9 | 9 | €0.89 | €8.01 | €8.01
Kitlijm voor bakken | In bezit | Gamma |  |  |  | 1 | 1 | €11.00 | €11.00 | €11.00
Regentonkraan voor bakken | In bezit | EuroShop |  |  |  | 1 | 1 | €4.50 | €4.50 | €4.50
Componenten PCB
Footprint | Value | References |  |  |  |  |  |  |  |  | Aanwezig op campus
Capacitor_SMD:C_0805_2012Metric_Pad1.18x1.45mm_HandSolder | 10u | C1 C7 C8 C9 C12 | 5 | 10 | 10 | 10 | 0
Capacitor_SMD:C_0805_2012Metric_Pad1.18x1.45mm_HandSolder | 100n | C2 C3 C10 C11 | 4 | 8 | 8 | 8 | 0
Capacitor_SMD:C_0805_2012Metric_Pad1.18x1.45mm_HandSolder | 1u | C5 | 1 | 2 | 2 | 2 | 0
Capacitor_SMD:C_0805_2012Metric_Pad1.18x1.45mm_HandSolder | 100u | C6 | 1 | 2 | 2 | 2 | 0
Diode_SMD:D_SOD-323_HandSoldering | D_Schottky | D1 D4 | 2 | 4 | 4 | 4 | 0
LED_SMD:LED_0805_2012Metric_Pad1.15x1.40mm_HandSolder | LED | D2 D3 | 2 | 4 | 4 | 4 | 0
Diode_SMD:D_SOD-123 | 1N4148W | D5 | 1 | 2 | 2 | 2 | 0
Connector_PinHeader_2.54mm:PinHeader_1x02_P2.54mm_Vertical | Conn_01x02 | J2 J3 | 2 | 4 | 4 | 4 | 0
Connector_PinHeader_2.54mm:PinHeader_1x04_P2.54mm_Vertical | Conn_01x04 | J4 J8 J14 J15 | 4 | 8 | 8 | 8 | 0
Connector_PinHeader_2.54mm:PinHeader_1x05_P2.54mm_Vertical | Conn_01x05 | J5 J7 | 2 | 4 | 4 | 4 | 0
Connector_PinHeader_2.54mm:PinHeader_1x10_P2.54mm_Vertical | Conn_01x10 | J6 J10 | 2 | 4 | 4 | 4 | 0
TerminalBlock_Phoenix:TerminalBlock_Phoenix_MKDS-1 | Screw_Terminal_01x02 | J9 J11 | 2 | 4 | 4 | 4 | 0
Connector_PinHeader_2.54mm:PinHeader_2x02_P2.54mm_Vertical | Conn_02x02_Counter_Clockwise | J12 | 1 | 2 | 2 | 2 | 0
Connector_PinHeader_2.54mm:PinHeader_1x03_P2.54mm_Vertical | Conn_01x03 | J13 | 1 | 2 | 2 | 2 | 0
Package_TO_SOT_SMD:SOT-23 | BSS138 | Q1 Q2 Q3 Q4 Q5 | 5 | 10 | 10 | 10 | 0
Resistor_SMD:R_0805_2012Metric_Pad1.20x1.40mm_HandSolder | 4K7 | R1 R2 R5 R6 | 4 | 8 | 8 | 8 | 0
Resistor_SMD:R_0805_2012Metric_Pad1.20x1.40mm_HandSolder | 1M | R3 | 1 | 2 | 2 | 2 | 0
Resistor_SMD:R_0805_2012Metric_Pad1.20x1.40mm_HandSolder | 10K | R4 R7 R8 R9 R10 R11 R12 R14 R16 | 9 | 18 | 18 | 18 | 0
Resistor_SMD:R_0805_2012Metric_Pad1.20x1.40mm_HandSolder | 1K | R13 R15 R17 | 3 | 6 | 6 | 6 | 0
434111043826:434111043826 | SW_Push | SW1 SW2 | 2 | 4 | 4 | 4 | 0
Watersysteem_Footprints_Library:MP1584_Module | MP1584_Module | U1 | 1 | 2 | 2 | 2 | 0
Package_TO_SOT_SMD:SOT-223-3_TabPin2 | AMS1117-3.3 | U2 | 1 | 2 | 2 | 2 | 0
RF_Module:ESP32-WROOM-32E | ESP32-WROOM-32E | U4 | 1 | 2 | 2 | 2 | 0
Verlichting en power | nt |  |  |  |  |  |  |  |  |  |  | Totaal Licht (Te bestellen)
Houten plaat | In bezit |  | 1 | 2 | 2 | 2 | 0 | €0.00 | €0.00 | €0.00 |  | €243.21
Main connector | In bezit | Mouser (https://www.mouser.be/ProductDetail/Schurter/KM00.1105.11?qs=h0lr9otJFD6kzO1nFMottA%3D%3D) | 0 | 1 |  | 1 | 1 | €13.35 | €13.35 | €13.35
Netsnoer | In bezit |  | 0 | 1 | 2 | 1 | 0 | - | - | -
Connectoren kast | In bezit | tinytronics (https://www.tinytronics.nl/nl/kabels-en-connectoren/connectoren/gx/gx12/gx12-4-connector-set) | 1 | 4 |  | 4 | 4 | €2.00 | €8.00 | €8.00
conectoren led pcb's | In bezit | tinytronics (https://www.tinytronics.nl/nl/kabels-en-connectoren/connectoren/schroefterminals/6-pin-schroef-terminal-block-connector-2.54mm-afstand) | 6 | 9 |  | 9 | 9 | €0.60 | €5.40 | €5.40
12V 3A supply voor water en planten | In bezit | Mouser (https://www.mouser.be/ProductDetail/TRACO-Power/TXN-35-112) | 0 | 1 |  | 1 | 1 | €16.52 | €16.52 | €16.52
24V 4.2 A supply voor verlichting | In bezit | Mouser (https://www.mouser.be/ProductDetail/TRACO-Power/TXN-100-124) | 0 | 1 |  | 1 | 1 | €23.81 | €23.81 | €23.81
Fuse voor main connector | In bezit | Mouser (https://www.mouser.be/ProductDetail/Schurter/43011403?qs=fxxZwZgTYwA8B4fs8Del4g%3D%3D&gad_source=5) | 1 | 1 |  | 1 | 1 | €5.22 | €5.22 | €5.22
Knop | In bezit | Mouser (https://eu.mouser.com/ProductDetail/TE-Connectivity-Alcoswitch/FSM4JSMATR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) | 1 | 2 |  | 2 | 2 | €0.30 | €0.60 | €0.60
Stencils | In bezit |  |  |  |  | 2 | 2 | €13.23 | €13.23 | €26.46
Thermische Lijm | In bezit | RS (https://benl.rs-online.com/web/p/adhesive-activators-primers-debonders/2384465?gb=s) |  |  |  | 1 | 1 | €10.25 | €10.25 | €10.25
Componenten LED-PCB
Led PCB | In bezit | PCBWay | 5 | 10 |  | 10 | 10 | €0.44 | €4.41 | €4.41 | 15 ipv 10?
Ver rode leds | In bezit | Ver rode leds Mouser (https://www.mouser.be/ProductDetail/Cree-LED/JE2835AFR-N-0001A0000-N0000001?qs=tlsG%2FOw5FFhxeS5Ond46kw%3D%3D) | 20 | 40 |  | 40 | 40 | €0.28 | €11.36 | €11.36
Rode leds | In bezit | Rode leds Mouser (https://www.mouser.be/ProductDetail/Cree-LED/JE2835AHR-N-0001A0000-N0000001?qs=tlsG%2FOw5FFjj3bMznpJhRA%3D%3D) | 30 | 60 |  | 60 | 60 | €0.27 | €15.96 | €15.96
Blauwe leds | In bezit | Blauwe leds Mouser (https://www.mouser.be/ProductDetail/Cree-LED/JE2835ARY-N-0002A0000-N0000001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) | 20 | 40 |  | 40 | 40 | €0.21 | €8.44 | €8.44
Heatsink led-PCB | In bezit | RS (https://benl.rs-online.com/web/p/heatsinks/9033096?gb=s) | 1 | 1 |  | 1 | 1 | €37.94 | €37.94 | €37.94
Thermal Pad led-PCB | In bezit | RS (https://benl.rs-online.com/web/p/thermal-pads/1745714?gb=s) | 1 | 2 |  | 2 | 2 | €21.81 | €43.62 | €43.62
Componenten Driver-PCB
Driver PCB | In bezit | PCBWay | 5 | 10 |  | 10 | 10 | €0.44 | €4.41 | €4.41
LDO voor ESP | In bezit | Mouser (https://www.mouser.be/ProductDetail/onsemi/NCP718BSN330T1G?qs=MLItCLRbWsy3SIiB9fjYCg%3D%3D) | 0 | 1 |  | 1 | 1 | €0.71 | €0.71 | €0.71
ESP-WROOM-32 | In bezit |  | 1 | 2 | 2 | 2 | 0 | €0.00 | €0.00 | €0.00
Connector driver pcb | In bezit | tinytronics (https://www.tinytronics.nl/nl/kabels-en-connectoren/connectoren/schroefterminals/2-pin-schroef-terminal-block-connector-2.54mm-afstand) | 1 | 2 |  | 2 | 2 | €0.30 | €0.60 | €0.60
Driver IC | In bezit | Mouser (https://www.mouser.be/ProductDetail/Diodes-Incorporated/AL1793AFE-13?qs=bKenfurwlskeSg5Tj2A9LQ%3D%3D) | 5 | 10 |  | 10 | 10 | €0.48 | €4.84 | €4.84
LDO voor ESP | In bezit | Mouser (https://www.mouser.be/ProductDetail/Texas-Instruments/UA78M33IKVURG3?qs=dP8SwFlKThxMmGpfgS%2FADQ%3D%3D) | 1 | 2 |  | 2 | 2 | €0.66 | €1.31 | €1.31
Driver Heatsink | In bezit |  |  |  |  |  |  |  |  |  | Nog aanvullen
Componenten per Driver-PCB
Footprint | Value | References
CAPC2013X95X50LL10T25 | Capacitor 100 nF +/-10% 50 V 0805 | C1, C2, C3, C4, C5 |  |  |  | 5
AL1793AFE13 |  | IC1_1, IC1_2, IC1_3 |  |  |  | 3
ESPWROOM32D |  | IC2 |  |  |  | 1
UA78M33IKVURG3 | Voltage Regulator | IC3 |  |  |  | 1
2828346 | Connector | J1_1, J1_2, J1_3 |  |  |  | 3
282834-2_1 | Connector | J2 |  |  |  | 1
61300411121 | Pin Header | P1 |  |  |  | 1
Resistors | Resistors | R1_1, R1_2, R1_3, R2_1, R2_2, R2_3, R3_1, R3_2, R3_3, R4_1, R4_2, R4_3, R5_1, R5_2, R5_3, R6_1, R6_2, R6_3, R7_1, R7_2, R7_3, R8 |  |  |  | 22
FSM4JSMATR | Micro Miniature Push Button Switch FSM JSM, 50 mA, -35 to 85 degC, 4-Pin SMD, RoHS, Tape and Reel | SW1 |  |  |  | 1
Componenten per LED-PCB
Footprint | Value | References
282834-6 | Connector | J0, J1 |  |  |  | 2
JE2835ARY-N-0002A0000-N0000001 | LED | B0, B1, B2 |  |  |  | 3
JE2835AFR-N-0001A0000-N0000001 | LED | FR0, FR1, FR2, FR3 |  |  |  | 4
JE2835AHR-N-0001A0000-N0000001 | LED | R0, R1, R2, R3, R4 |  |  |  | 5
KAST |  |  |  |  |  |  |  |  |  |  |  | Totaal Buitenkast (Te bestellen)
 |  |  |  |  |  |  |  |  |  |  |  | €312.59
Hout binnenkast (schatting) | Resthout
 | afmetingen (mm) | aantal
 | 2000x600x18 | 4
Oude laden |  | 6
Gextrudeerde aluminium profielen
 | afmetingen (mm) | aantal
 | 2200x90x45 | 4
 | 640x90x45 | 4
 | 550x90x45 | 4
Wieltjes
 | Draaiend | 2
 | Vast | 2
Houtschroeven
DEUR
 | lengte | aantal
Deurkader (sectie 18mm x 60mm)
 | 2.294 | 2 | 4.588
 | 2.330 | 2 | 4.660
 | 0.732 | 2 | 1.464
 | 2.194 | 1 | 2.194
 | 0.560 | 1 | 0.560
 | 0.736 | 1 | 0.736
 | Totaal: | lengte | 14.202 | m
 |  | breedte | 0.060 | m
 |  | opp | 0.852 | m2 | €95.79 | eenheidsprijs/m2 Eurabo
 |  |  | prijs |  | €81.62
 |  |  | aantal
Klepscharnieren |  |  | 14 | €4.69 | €65.66 |  | Scharnieren (https://www.meubelbeslagonline.nl/klepscharnier-staal-vernikkeld-gepolijst)
MMLAB plaat 840 x 1200 x 6
 |  |  | 2 | €42.12 | €84.24
ZIJKANTEN: fineerplaten op kaders
 |  | breedte | 0.730 | m
 |  | hoogte | 2.330 | m
 |  | aantal | 2.000
 |  | opp | 3.402 | m2 | €23.83 | eenheidsprijs CRAS Merelbeke
 |  |  | prijs |  | €81.06
Blachon |  |  |  |  |  |  | Blanchon (https://baticolage.com/products/blanchon-huile-environnement-5l?variant=39781262229678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)
 |  |  |  |  | -

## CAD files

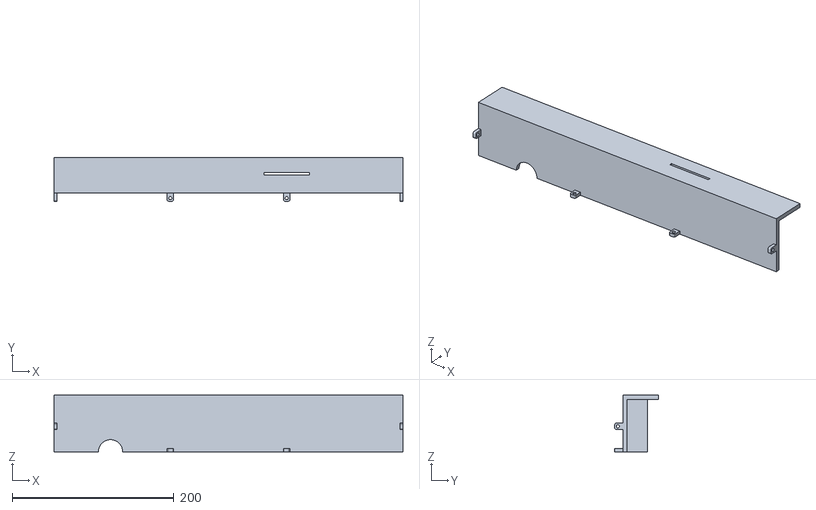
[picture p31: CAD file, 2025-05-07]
assets/img/Plantenbak/plantenbak.stl
432.0 x 54.0 x 70.0

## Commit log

2025-04-09 Fix config and homepage
    Temporary switch to simpler theme
2025-04-16 Corrected layout power light
2025-04-22 Afbeelding PCB Watersysteem
2025-04-22 tekst bij PCB, verdere aanvullingen
2025-04-24 Update Logboek.md
    Team Water, callibration of probes
2025-05-03 Update webpagina water en power
    Aanvulling webpagina water en power => energie verbruik.
2025-05-03 Changes to Power.md
2025-05-03 Ibom toegevoegd
    proberen om ibom embedded in tab te krijgen
2025-05-03 Changed location of ibom to bom location + Removed duplicate image
2025-05-04 Extra info moved to files
    [BOM.xlsx]
2025-05-04 Commit BOM
    [BOM.xlsx]
2025-05-05 Update Power.md
    verbetering URL
2025-05-05 dt foutje 🤭
2025-05-06 Update Water.md
    pH probe -> analoog
2025-05-06 Update Water.md
    2 status leds -> 1 package
2025-05-06 duidelijker voor een leek
2025-05-06 Update Logboek.md
    Toevoeging team power
2025-05-06 Update Water.md
    tubes: binnendiameter en buitendiameter
2025-05-06 Update Power.md
    Aanpassingen op de site voor team power
2025-05-06 Add Image
    afbeelding van connecties pcb toegevoegd
2025-05-06 Update Plantenbak.md met research over keuze sensoren
2025-05-06 Fixed Images Power.md
2025-05-06 Fixed mistake in BOM
    [BOM.xlsx]
2025-05-07 bronvermelding in power.md
2025-05-11 Replaced image with better cut out
2025-05-11 Moved BOM
    [BOM.xlsx]
2025-05-12 Changed LED to led
2025-05-12 Changes for uniformity power.md
2025-05-17 Added link to probe characteristics
